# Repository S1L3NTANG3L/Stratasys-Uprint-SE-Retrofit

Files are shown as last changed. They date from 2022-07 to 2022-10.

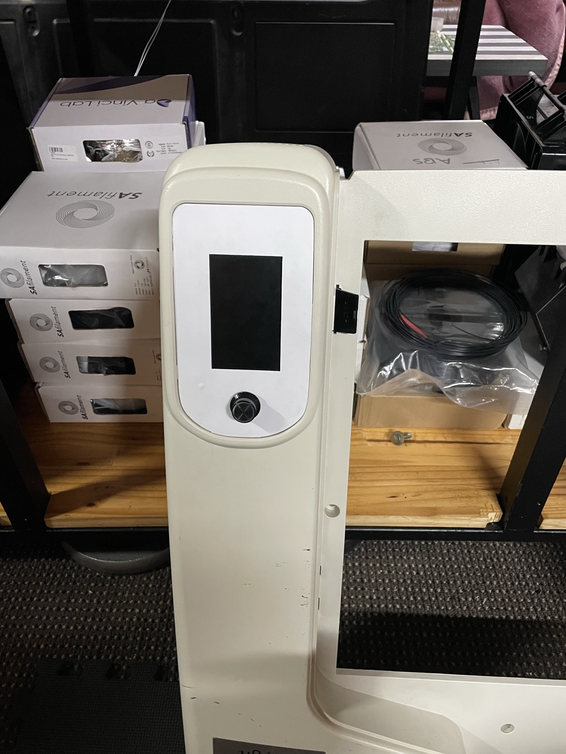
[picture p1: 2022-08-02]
Media/IMG_0999.JPEG

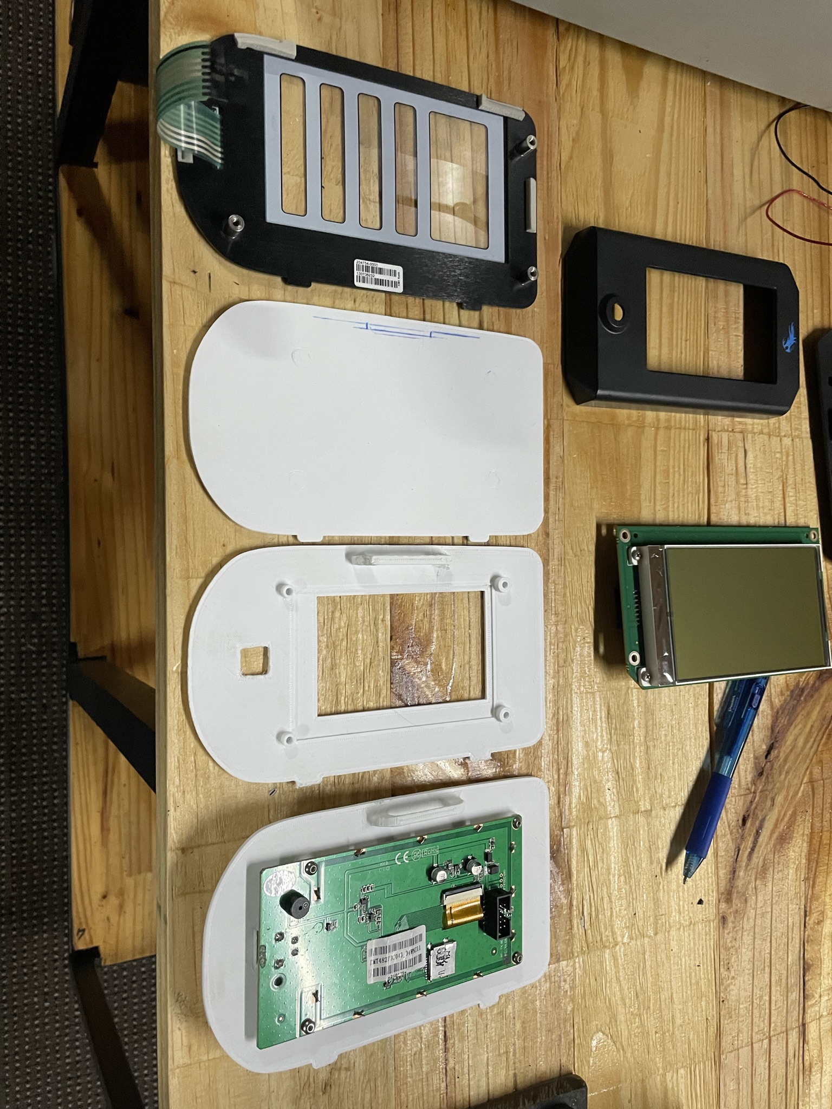
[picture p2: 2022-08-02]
Media/IMG_0998.JPEG

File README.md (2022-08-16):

# Stratasys-Uprint-SE-Retrofit
WORK IN PROGRESS! Retrofitting a stratasys Uprint SE to run marlin or klipper and keep the majority of the original functionality.

Extra Resources:<br />
https://forum.duet3d.com/topic/10982/stratasys-uprint-retrofit-finally-complete/19<br />
https://wiki.cnc.xyz/Stratasys_uPrint_Retrofit<br />
https://forum.duet3d.com/topic/12647/another-stratasys-uprint-retrofit<br />
https://vectormfg.net/stratasys-uprint-duet-wifi-conversion/<br />
https://www.stratasys.com/-/media/files/documentation/fdm/uPrint-SE-and-uPrint-SE-Plus/User-Guide/uPrint-SE-uPrint-SE-Plus-User-Guiden\<br />



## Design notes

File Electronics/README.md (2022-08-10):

#Electronics
All the designs for pcbs that need to be custom made are stored here.

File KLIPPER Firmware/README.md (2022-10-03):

# Klipper Firmware
* Work in progress, will update as I go
## Need to follow [this](https://klipperscreen.readthedocs.io/en/latest/Hardware/?h=ori#screen-rotation) to get the klipper screen rotation and touchscreen matrix setup correctly.</br>
`sudo nano /usr/share/X11/xorg.conf.d/90-monitor.conf`</br>
Section "Monitor"</br>
    Identifier "HDMI-1"</br>
    Option "Rotate" "right"</br>
    Option "PreferredMode" "800x400"</br>
EndSection</br>
`sudo service KlipperScreen restart`</br>
`DISPLAY=:0 xinput`</br>
`sudo nano /usr/share/X11/xorg.conf.d/40-libinput.conf`</br>
Section "InputClass"</br>
        Identifier "libinput touchscreen catchall"</br>
        MatchIsTouchscreen "on"</br>
        MatchDevicePath "/dev/input/event*"</br>
        Driver "libinput"</br>
        Option "TransformationMatrix" "0 1 0 -1 0 1 0 0 1"</br>
EndSection</br>
`sudo service KlipperScreen restart`</br>
## Need to follow [this](https://github.com/bigtreetech/CB1/issues/44#issuecomment-1264733456) to get the gpio pins working if you get an parsing error.

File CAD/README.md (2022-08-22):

All the design files for the custom made parts.<br />
Hotend blocks that fir original head but are supervolcano and E3D V6 compatible.<br />
<br />
Nema 17 extuder mount that fits in the same place as the old Maxon dc motor.<br />
<br />

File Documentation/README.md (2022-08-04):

Bunch of documents I compiled around some of the parts in the printer.

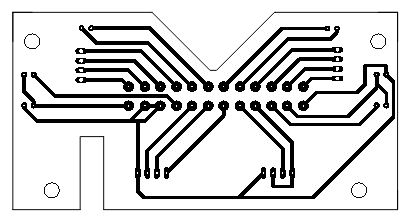
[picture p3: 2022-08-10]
Electronics/Toggle Head PCB/PCB_PCB_Stratasys UPRINT Toggle Head Board_2022-08-10.png

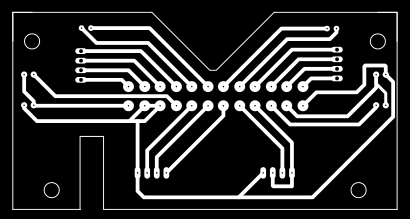
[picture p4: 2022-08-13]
Electronics/Toggle Head PCB/PCB_PCB-Stratasys-UPRINT-Toggle-Head-Board_2022-08-10.png

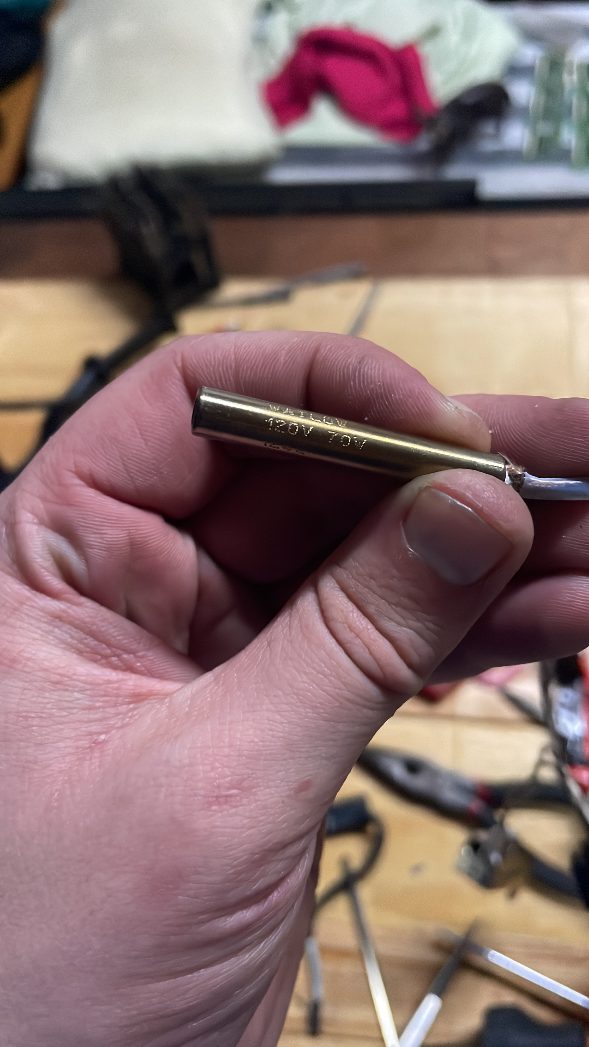
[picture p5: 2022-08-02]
Media/E2CDCEC5-779F-4118-A0D4-56C21CC2E0AF.jpg

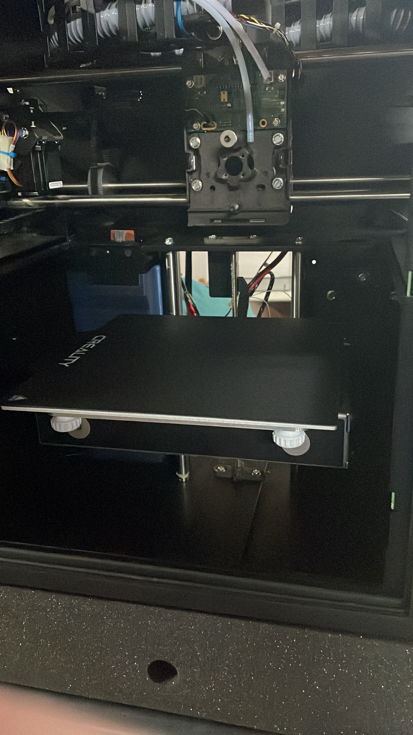
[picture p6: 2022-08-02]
Media/7F880011-2E3F-456F-A0A6-C916DF5192D8.jpg

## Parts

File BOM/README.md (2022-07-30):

The Bill of Materials is in SOUTH AFRICAN RANDS and contains some links to local suppliers, will update with international suppliers when I have time.

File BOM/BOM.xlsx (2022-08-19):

Amount | Product | Link | Price Per Piece | Sub Total | Comment
1 | Relay 8 Channel | https://www.pishop.co.za/store/eight-channel-5v-dc-relay-module | 129.9 | R 129.90 | To control extras.
1 | 688ZZ Ball Bearing | https://www.robotics.org.za/688ZZ | 30 | R 30.00 | For the custom extruder.
1 | Round Stock Aluminum | Local Seller : No Website | 342.48 | R 342.48 | For the custom extruder parts.
2 | Trianglelab PT100 4-wire Kit | https://www.aliexpress.com/item/1005003923279506.html?spm=a2g0o.cart.0.0.337038daCg3QUq&mp=1 | R 422.10 | R 844.20 | One for each hotend.
1 | SSR-25DA Solid State Relay 3-32V Control 25A | https://www.rabtron.co.za/solid-state-relays/10419-ssr-25da-solid-state-relay-3-32v-control-25a.html | R 92.00 | R 92.00 | To control the enclosure heaters.
1 | BIGTREETECH Manta M8P Control Board with CB1 | https://biqu.equipment/collections/control-board/products/manta-m4p-m8p | R 1331.99 | R 1331.99
2 | BTT SFS V1.0 Smart Filament Sensor Detection | https://biqu.equipment/collections/expansion-board/products/btt-sfs-v1-0-smart-filament-sensor-detection-stuck-blocking-filament-module | R 215.00 | R 430.00
4 | BIGTREETECH TMC2226 V1.0 Stepper Motor Driver | https://biqu.equipment/collections/driver-board/products/bigtreetech-tmc2226-v1-2-stepper-motor-driver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 | R 90.00 | R 360.00
1 | Din Rail TS35 | Local Seller : No Website | R 39.14 | R 39.14 | Comes in 2 meter sections.
25 | Din Rail Terminal | Local Seller : No Website | R 9.61 | R 240.25
7 | Din Rail Terminal End Cover | Local Seller : No Website | R 4.90 | R 34.30
2 | Din Rail Endstop | Local Seller : No Website | R 12.40 | R 24.80
1 | Replacement Heated Bed for BIQU B1 | https://www.diyelectronics.co.za/store/beds-heaters/3374-replacement-heated-bed-for-biqu-b1.html | R 300.00 | R 300.00
1 | Glass Print Bed for Ender 3 | https://www.diyelectronics.co.za/store/beds-heaters/2032-glass-print-bed-for-ender-3.html | R 50.00 | R 50.00
4 | BRASS NICKEL PLATED M3x35mm FEMALE TO FEMALE 5AF | https://www.mantech.co.za/ProductInfo.aspx?Item=14M0341-H | R 5.57 | R 22.28 | For the custom extruder.
1 | Creality CMagnet FlexPlate 235x235mm | https://www.diyelectronics.co.za/store/beds-heaters/2184-creality-cmagnet-flexplate-235x235mm.html | R 180.00 | R 180.00
2 | Trianglelab 3D Printer 6*47.5MM 80W Heater Cartridge | https://www.aliexpress.com/item/4001145708192.html?spm=a2g0o.cart.0.0.188f38daN1PcVJ&mp=1 | R 76.93 | R 153.86
Total |  |  |  | R 4605.20
 | *Wire, crimps and misc parts not listed*

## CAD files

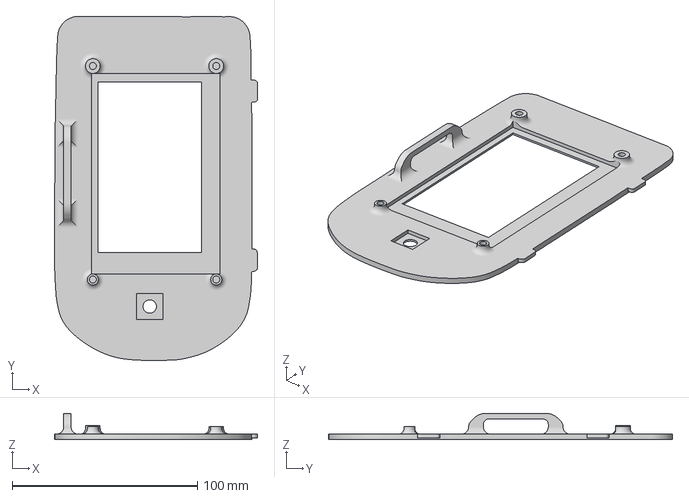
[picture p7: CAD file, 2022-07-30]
CAD/Screen Cover (Ender 3 V2 Screen).3mf
109.6 x 185.6 x 14.2 mm

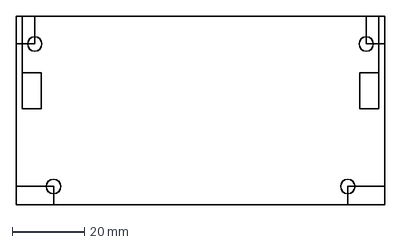
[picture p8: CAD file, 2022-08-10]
Electronics/Toggle Head PCB/Umbilical.dxf
101.8 x 52.2 mm

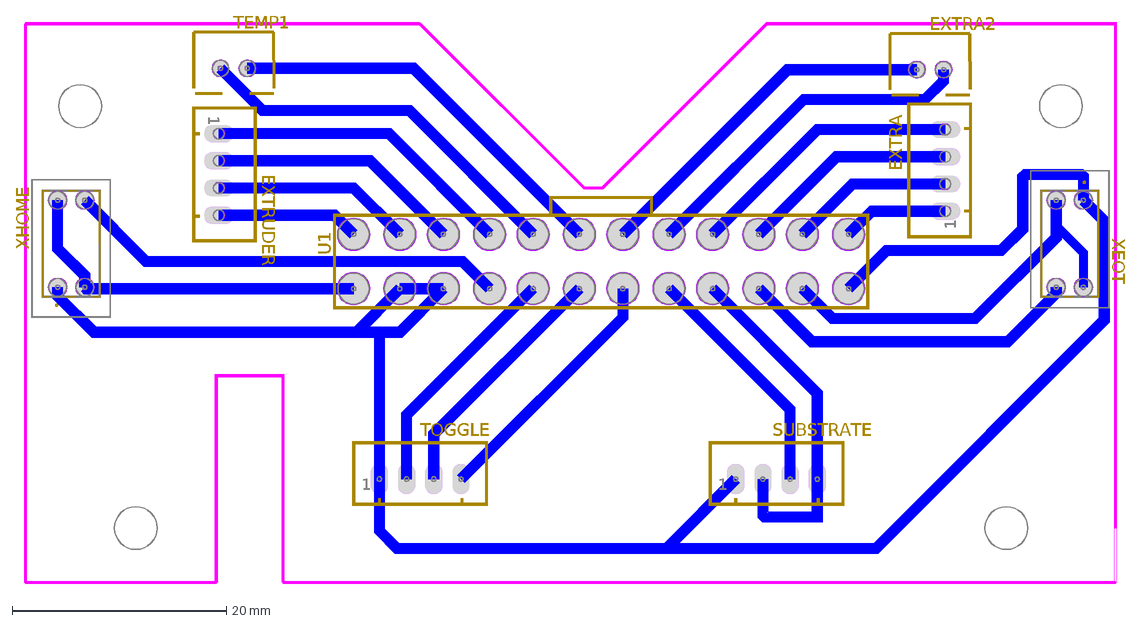
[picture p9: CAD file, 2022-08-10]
Electronics/Toggle Head PCB/PCB_Stratasys UPRINT Toggle Head Board_2022-08-10.dxf
EXTRA
1
EXTRA2
EXTRUDER
TEMP1
U1
SUBSTRATE
TOGGLE
XEOT
XHOME

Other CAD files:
CAD/Dondol Bar v4.f3d
CAD/Extruder Assembly v17.f3d
CAD/Hot Bed Adjustment Nuts.f3d
CAD/Uprint SE Heated Bed Adapter Plate.f3d
CAD/Uprint SE Screen.f3d
CAD/Uprint Std E3D Nozzle Heater Block v17.f3d
CAD/Uprint Super Volcano Heater Block v2.f3d

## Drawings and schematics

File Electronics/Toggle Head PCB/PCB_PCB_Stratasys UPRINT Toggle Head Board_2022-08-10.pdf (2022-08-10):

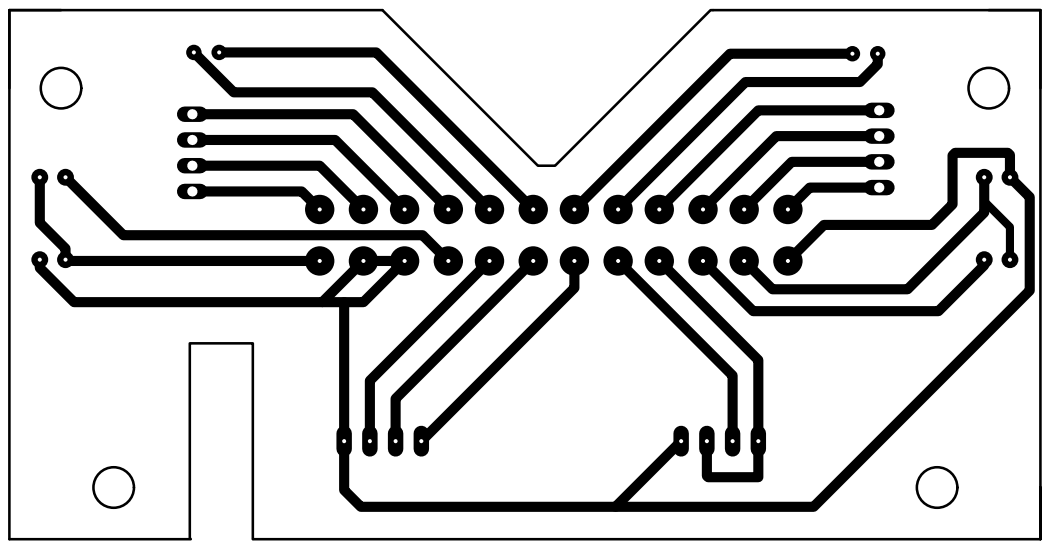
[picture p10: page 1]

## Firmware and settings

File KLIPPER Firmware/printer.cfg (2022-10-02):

[include mainsail.cfg]

# This file contains common pin mappings for the BIGTREETECH Manta M8P
# To use this config, the firmware should be compiled for the
# STM32G0B1 with a "8KiB bootloader" and USB communication.

# See docs/Config_Reference.md for a description of parameters.
#####################################################################################
#------------------------------------PRINTER----------------------------------------#
#####################################################################################
[mcu]
serial: /dev/serial/by-id/usb-Klipper_stm32g0b1xx_hurakan-if00
restart_method: command

[printer]
kinematics: cartesian
max_velocity: 300
max_accel: 3000
max_z_velocity: 5
max_z_accel: 100

[virtual_sdcard]
path: ~/gcode_files

[display_status]

[pause_resume]

[respond]
default_type: command

[temperature_sensor CB1]
sensor_type: temperature_host
sensor_path: /sys/class/thermal/thermal_zone0/temp
min_temp: 0
max_temp: 100

[temperature_sensor Manta]
sensor_type: temperature_mcu
sensor_mcu: mcu
min_temp: 0
max_temp: 100

#####################################################################################
#------------------------------------MOVEMENT---------------------------------------#
#####################################################################################
[stepper_x]
step_pin: PE2
dir_pin: !PB4
enable_pin: !PC11
microsteps: 16
rotation_distance: 30.00187512
endstop_pin: PF3
position_endstop: 0
position_max: 238
homing_speed: 15

[stepper_y]
step_pin: PF12
dir_pin: !PF11
enable_pin: !PB3
microsteps: 16
rotation_distance: 11.94029851
endstop_pin: PF4
position_endstop: 0
position_max: 266
homing_speed: 15

[stepper_z]
step_pin: PD7
dir_pin: PD6
enable_pin: !PF10
microsteps: 16
rotation_distance: 3.162086582
endstop_pin: PF5
position_endstop: 0
position_max: 5
position_min: -330
homing_speed: 8
second_homing_speed: 3
homing_retract_dist: 3

# Motor4
# The M8P only has 4 heater outputs which leaves an extra stepper
# This can be used for a second Z stepper, dual_carriage, extruder co-stepper,
# or other accesory such as an MMU
#[stepper_]
#step_pin: PD3
#dir_pin: PD2
#enable_pin: PD5
#endstop_pin: PC0
#...

# Motor6
#[extruder1]
#step_pin: PA10
#dir_pin: PD15
#enable_pin: !PA15
#heater_pin: PB5 # HE1
#sensor_pin: PA2 # T1
#...

# Motor7
#[extruder2]
#step_pin: PD12
#dir_pin: PD11
#enable_pin: !PD14
#heater_pin: PB6 # HE2
#sensor_pin: PA3 # T2
#...

# Motor8
#[extruder3]
#step_pin: PD10
#dir_pin: PD8
#enable_pin: !PD9
#heater_pin: PE1 # HE3
#sensor_pin: PA4 # T3
#...


#####################################################################################
#------------------------------------Extruders--------------------------------------#
#####################################################################################
#NOT DONE
#[extruder material_0]
#step_pin: PD3
#dir_pin: PD2
#enable_pin: PD5
#microsteps: 16
#rotation_distance: 33.500
#nozzle_diameter: 0.4
#filament_diameter: 1.75
#heater_pin: PE3 
#sensor_type: Generic 3950
#control: pid
#min_temp: 0
#max_temp: 350

[filament_switch_sensor material_0]
switch_pin: PC6

[filament_switch_sensor material_1]
switch_pin: PA9

#####################################################################################
#------------------------------------HEATERS && FANS--------------------------------#
#####################################################################################
#NOT DONE
[heater_bed]
heater_pin: PB7
sensor_pin: PA0
sensor_type: EPCOS 100K B57560G104F
control: watermark
min_temp: 0
max_temp: 130

[heater_generic chamber_heater]
gcode_id: M141
heater_pin: PB6
sensor_pin: PA1
sensor_type: EPCOS 100K B57560G104F
control: watermark
min_temp: 0
max_temp: 75

[verify_heater chamber_heater]
#max_error: 120
check_gain_time:80
hysteresis: 5
heating_gain: 2

#[heater_fan heaters_fan]
#pin: PE6
#heater: extruder
#heater_temp: 50.0

[fan_generic left_fan]
pin: PC12
max_power: 1.0
#fan_speed: 1.0
#idle_timeout:600
#idle_speed:0.6
#heater:chamber_heater

[fan_generic right_fan]
pin: PE0
max_power: 1.0
#fan_speed: 1.0
#idle_timeout:600
#idle_speed:0.6
#heater:chamber_heater

#[heater_fan fan3]
#pin: PE5

#[heater_fan fan4]
#pin: PE4
#tachometer_pin: PC13

#[heater_fan fan5]
#pin: PB8
#tachometer_pin: PC14

#[heater_fan fan6]
#pin: PB9
#tachometer_pin: PC15

#####################################################################################
#------------------------------------TMC2209----------------------------------------#
#####################################################################################

[tmc2209 stepper_x]
uart_pin: PC10
#diag_pin: ^PF3
run_current: 1.4
stealthchop_threshold: 999999
#driver_SGTHRS: 150

[tmc2209 stepper_y]
uart_pin: PF13
#diag_pin: ^PF4
run_current: 1.4
stealthchop_threshold: 999999
#driver_SGTHRS: 150

[tmc2209 stepper_z]
uart_pin: PF9
#diag_pin: ^PF5
run_current: 0.8
stealthchop_threshold: 999999
#driver_SGTHRS: 30

##[tmc2209 extruder]
##uart_pin: PD4
##diag_pin: PC0
##run_current: 0.8
##stealthchop_threshold: 999999

#[tmc2209 extruder]
#uart_pin: PD0
#run_current: 0.800
#stealthchop_threshold: 999999

#[tmc2209 extruder1]
#uart_pin: PF8
#run_current: 0.800
#stealthchop_threshold: 999999

#[tmc2209 extruder2]
#uart_pin: PD13
#run_current: 0.800
#stealthchop_threshold: 999999

#[tmc2209 extruder3]
#uart_pin: PC7
#run_current: 0.800
#stealthchop_threshold: 999999

#####################################################################################
#-------------------------------BED LEVELING PROBE----------------------------------#
#####################################################################################
#NOT DONE
[probe]
pin: ^PB1
z_offset: 5.968 #Measure per your specific setup
x_offset: 6 # negative = left of the nozzle
y_offset: 35 # negative = in front of of the nozzle
speed: 5.0
lift_speed: 15.0
sample_retract_dist: 1
samples: 2
samples_tolerance_retries: 6

[bed_mesh]
speed: 300
horizontal_move_z: 6
mesh_min: 8,30
mesh_max: 223,201
probe_count: 7,7
relative_reference_index: 12
algorithm: bicubic
fade_start: 1
fade_end: 10
#fade_target:
#   The z position in which fade should converge. When this value is set
#   to a non-zero value it must be within the range of z-values in the mesh.
#   Users that wish to converge to the z homing position should set this to 0.
#   Default is the average z value of the mesh.
split_delta_z: 0.015
#   The amount of Z difference (in mm) along a move that will
#   trigger a split. Default is .025.
move_check_distance: 3
#   The distance (in mm) along a move to check for split_delta_z.
#   This is also the minimum length that a move can be split. Default
#   is 5.0.
mesh_pps: 4,4
#   A comma separated pair of integers (X,Y) defining the number of
#   points per segment to interpolate in the mesh along each axis. A
#   "segment" can be defined as the space between each probed
#   point. The user may enter a single value which will be applied
#   to both axes.  Default is 2,2.
#bicubic_tension: .2
#   When using the bicubic algorithm the tension parameter above
#   may be applied to change the amount of slope interpolated.
#   Larger numbers will increase the amount of slope, which
#   results in more curvature in the mesh. Default is .2.

[gcode_macro AUTO_BED_MESH]
gcode:
    G28
    PROBE_OUT
    BED_MESH_CALIBRATE
    G1 Y0 F20000
    PROBE_IN

[gcode_macro PROBE_OUT]
gcode:
    G90
    G1 Z6.5
    G1 X245 F20000
    G1 Z0
    G4 P300
    G1 Z20
    G1 X0

[gcode_macro PROBE_IN]
gcode:
    G90
    G1 Z20
    G1 X245 F20000
    G1 Z0
    G4 P300
    G1 X235 F1000
    G1 Z5
    G4 P300
    G1 X0 F20000
    G1 Z0

#####################################################################################
#------------------------------------OTHER PINS-------------------------------------#
#####################################################################################

[board_pins]
aliases:
    # EXP1 header
    EXP1_1=PE9, EXP1_2=PE10,
    EXP1_3=PE11, EXP1_4=PE12,
    EXP1_5=PE13, EXP1_6=PE14,    # Slot in the socket on this side
    EXP1_7=PE15, EXP1_8=PB10,
    EXP1_9=<GND>, EXP1_10=<5V>,

    # EXP2 header
    EXP2_1=PB14, EXP2_2=PB13,
    EXP2_3=PF7, EXP2_4=PB12,
    EXP2_5=PE7, EXP2_6=PB11,      # Slot in the socket on this side
    EXP2_7=PE8, EXP2_8=<RST>,
    EXP2_9=<GND>, EXP2_10=PC5

# See the sample-lcd.cfg file for definitions of common LCD displays.

#[bltouch]
#sensor_pin: PB2
#control_pin: PB1

# Proximity switch
#[probe]
#pin: PF6

#[output_pin ps_on_pin]
#pin: PC3

#[neopixel my_neopixel_1]
#pin: PC6

#[neopixel my_neopixel_2]
#pin: PA9

#[hall_filament_width_sensor]
#adc1: PC5
#adc2: PB0
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

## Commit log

2022-07-30 Ender 3 V2 Screen Implementation
    [Screen Cover.3mf]
2022-07-31 Add files via upload
    Dondolo shift arm replacement.
    [Dondol.3mf]
2022-08-02 Add files via upload
    Uprint Super Volcano Heat Block
    [Super Volcano Heater Block v4.f3d]
2022-08-04 Design file changes
    [Dondol Bar v4.f3d, Dondol.3mf, Screen Cover (Ender 3 V2 Screen).3mf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]
2022-08-10 PCB Design
    [PCB_Stratasys UPRINT Toggle Head Board_2022-08-10.dxf, Umbilical.dxf]
2022-08-10 Hotend V11
    [Super Volcano Heater Block v11.f3d]
2022-08-14 Cad Changes
    [Super Volcano Heater Block v10.f3d, Super Volcano Heater Block v11.f3d, Super Volcano Heater Block v9.f3d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]
2022-08-16 Extruder Sleeve Design
    [Extruder Gear Sleeve v3.f3d]
2022-08-17 New Extruder Assembly
    [Extruder Assembly v3.f3d, Extruder Gear Sleeve v3.f3d]
2022-08-17 Cad updates
    [Extruder Assembly v3.f3d, Extruder Assembly v9.f3d, Uprint Std E3D Nozzle Heater Block v17.f3d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]
2022-08-17 Extruder update
    [Extruder Assembly v12.f3d, Extruder Assembly v9.f3d]
2022-08-19 BOM Update
    [BOM.xlsx]
2022-09-22 HDMI5 Screen add
    [printer.cfg]
2022-09-23 Screen CAD Update
2022-10-02 Major config changes
    [mainsail.cfg, printer.cfg]
